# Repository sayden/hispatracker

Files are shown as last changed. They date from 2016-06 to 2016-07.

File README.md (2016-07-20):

# WIP hispatracker

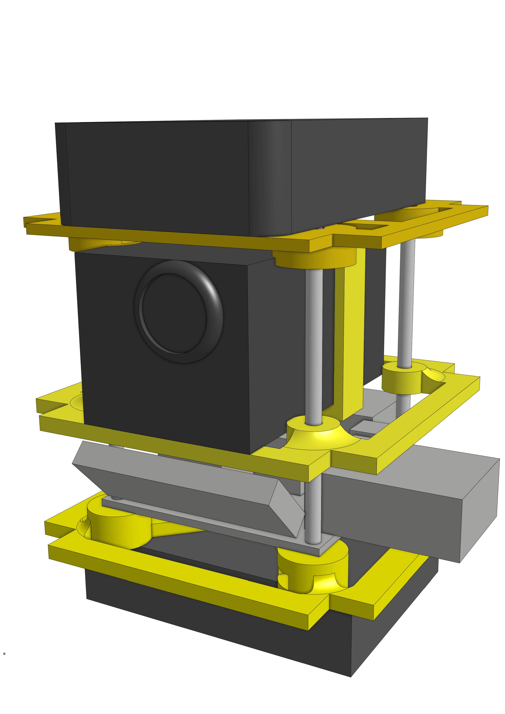
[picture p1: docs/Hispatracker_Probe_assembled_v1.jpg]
Hispatracker


An Arduino based project for High Altitude Ballooning. APRS tracker, 2xGPS, temperature and pressure. It still lacks SD logging and an external temperature sensor as the sketch was running out of memory. We are working in a improved version with the atmega1284p-pu to achieve this goals (and maybe some more).

## Sensors and libraries in use

### GPS and Altitude: Ublox Neo6M
We strongly recommend to use SlashDevin's [NeoGPS](https://github.com/SlashDevin/NeoGPS) library for its low memory footprint and awesome documentation. The alternative, TinyGPS is too heavy for most applications in a common Arduino (atmega328p-pu).

Our GPS is the Ublox Neo-6m with a performance of 50.000 meters (yes, 50 km) of altitude, 2.5 meters of accuracy and works at 3.3v

### BMP085 Temperature, altitude and pressure sensor

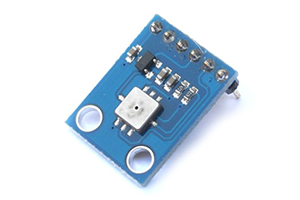
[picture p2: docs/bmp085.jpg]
BMP085


Good compromise between price and capabilities but with a altitude limit of 9000 meters over the sea (27000 feet). It works at 3.3v

### RF Transmission: Radiometrix HX1

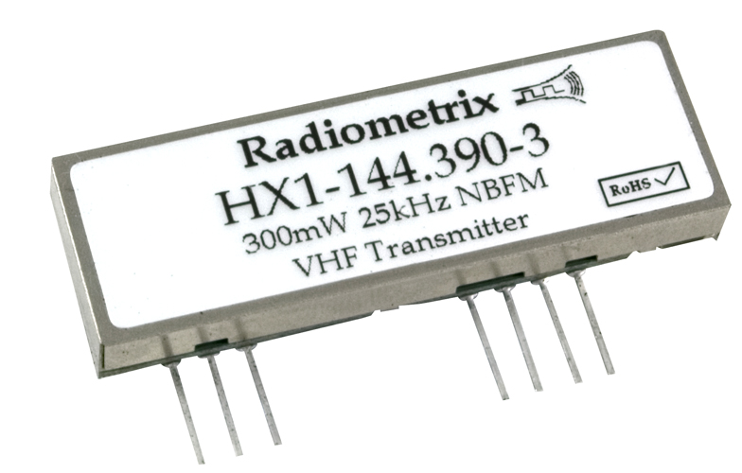
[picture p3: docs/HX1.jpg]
HX1


We think that maybe this was a mistake. It has a usable range over 10km and a consumption of 140mA. It has a transmit power of 300mW so you probably need HAM license to use it. Also it works at 5v, being the only module with this voltage needs, it has introduce a need of raising the VIN to, at least 6v so that we provide a regulated supply of 5v to the Radio and 3.3v to the rest of the module. Also it has force us to use a logic level converter to communicate to it. 

The good part is that it was the only able to transmit at 144.800 to use the APRS network. So we can use the network to track our payload with webs like [aprs.fi](http://aprs.fi).

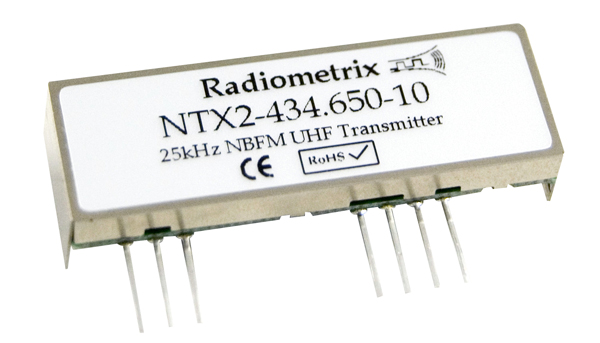
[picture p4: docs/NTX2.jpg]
NTX2


The alternative was to use the NTX2 transmitter. This transmitter is license free with a usable range of 500m (thats a 5% of the power of the HX1). It just transmits on 434.075MHz, 434.650MHz and 458.700MHz so it's not in the APRS network. It has a voltage regulator and you can feed it with 3.3 volts. We'll play with it in the future.

### Arduino Pro Mini 3.3v

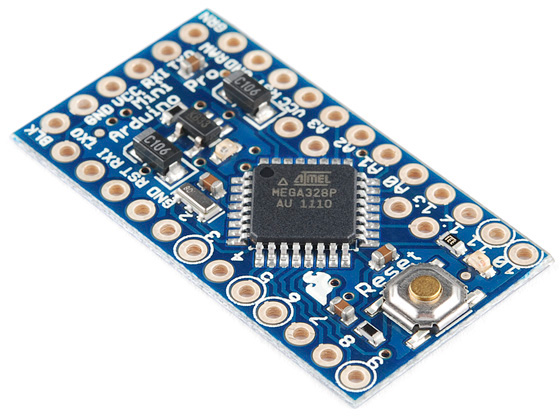
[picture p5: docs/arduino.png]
arduino


Finally, our brain is controlled by an Arduino Pro Mini running at 3.3v

### PCB
Our PCB has been specifically design to fit our needs. You'll find the files in the eagle folder. The PCB has been produce in Seeedstudio. It's 5x5 cm.

### Hardware

Check the [docs](docs) folder. We have used a Prusa i3 3D printer to build the frame of the probe. Basically supports for the batteries, camera, PCB and GPS tracker. STL's will be available in the hardware folder soon as well as in Thingiverse.

The supports are 7x7cm with holes to support the PCB of 5x5cm. In our first tests it reaches a height of 107mm.

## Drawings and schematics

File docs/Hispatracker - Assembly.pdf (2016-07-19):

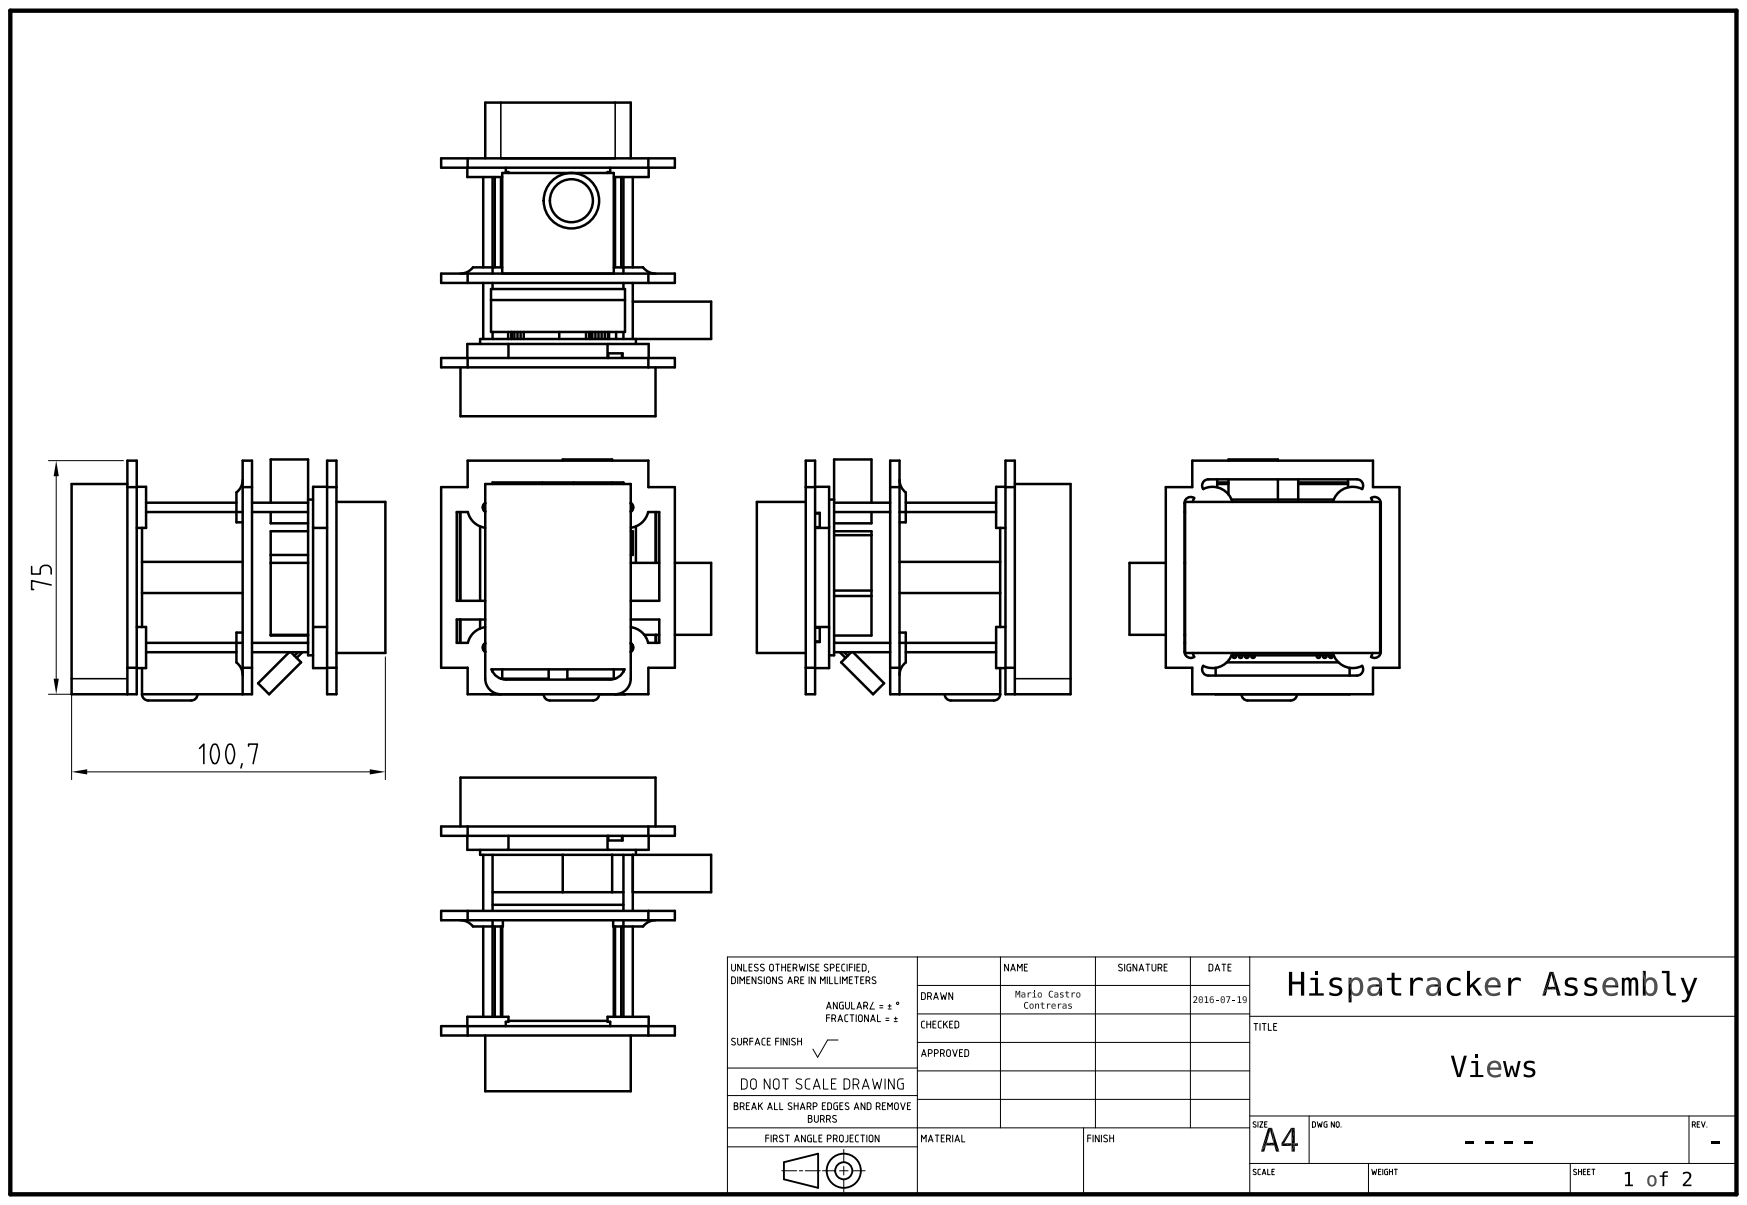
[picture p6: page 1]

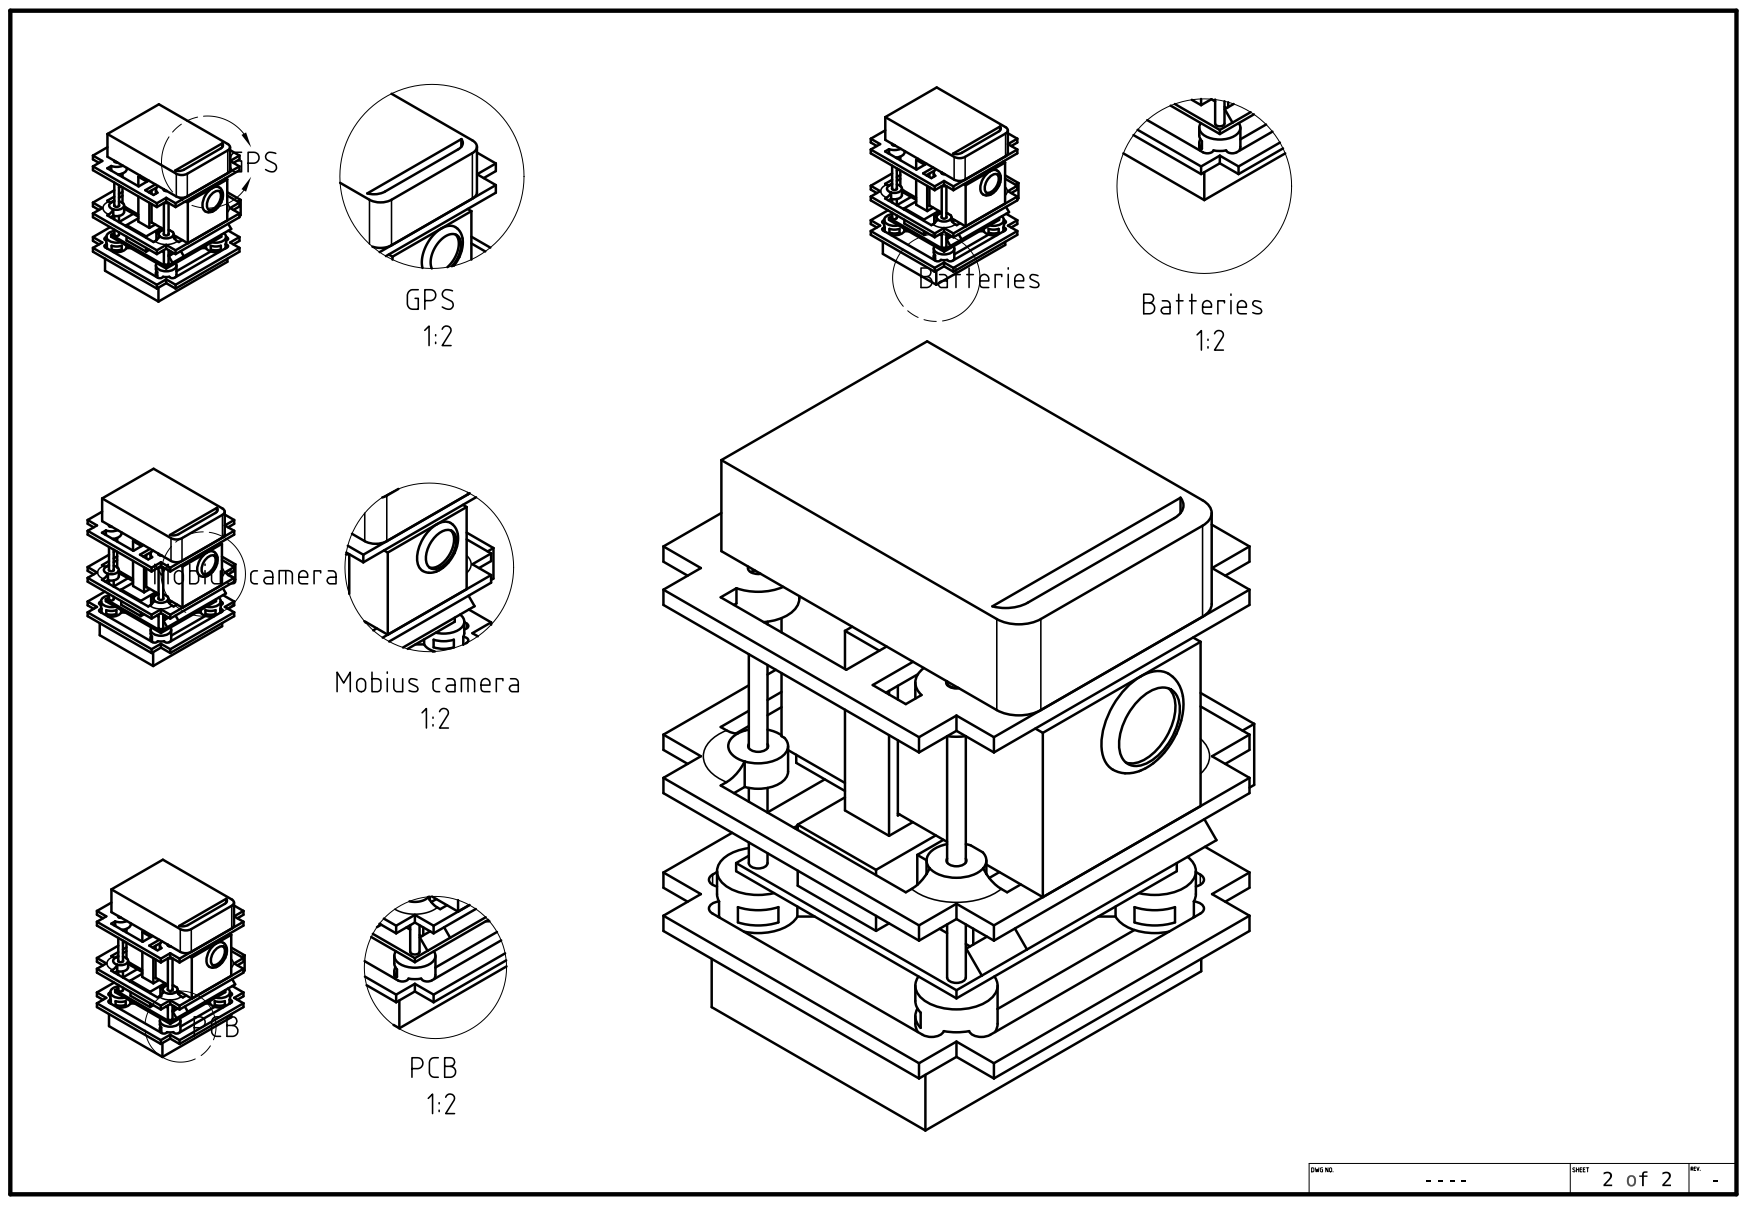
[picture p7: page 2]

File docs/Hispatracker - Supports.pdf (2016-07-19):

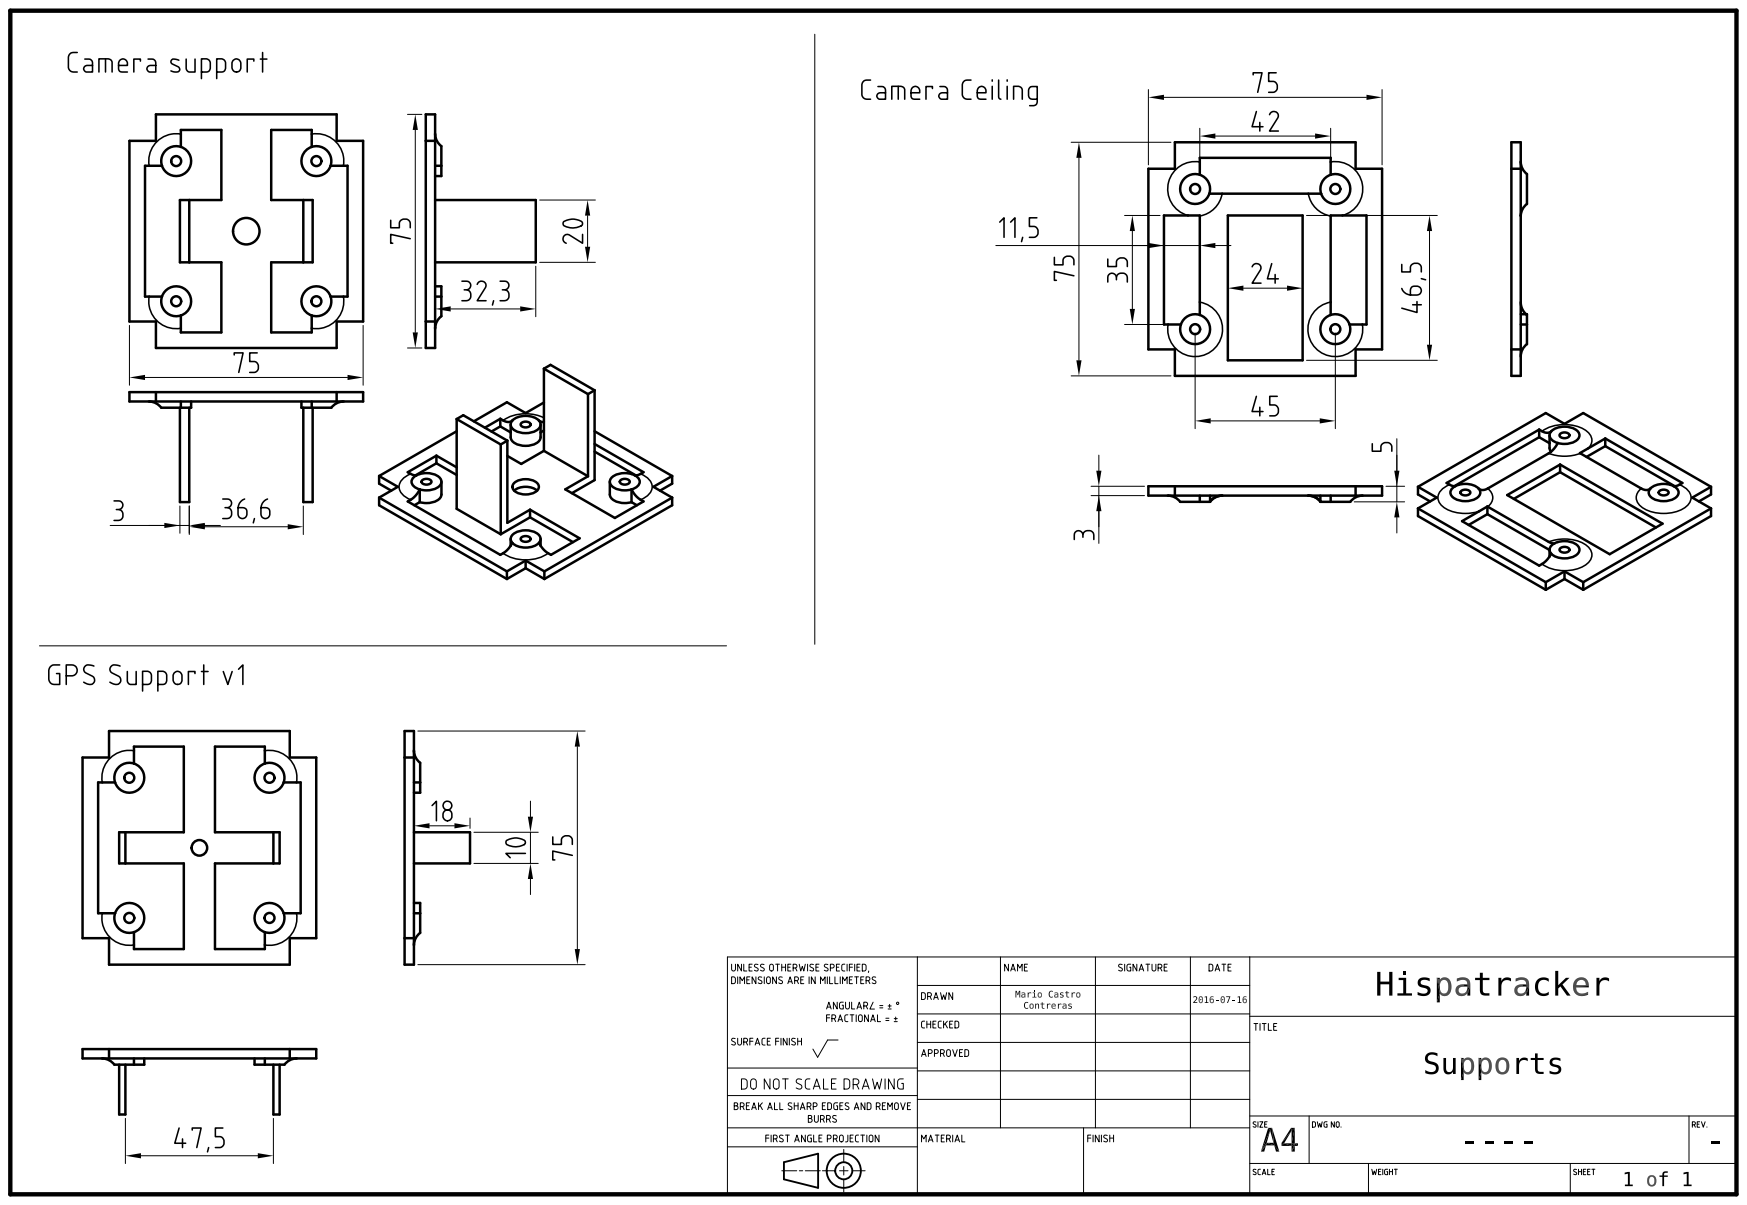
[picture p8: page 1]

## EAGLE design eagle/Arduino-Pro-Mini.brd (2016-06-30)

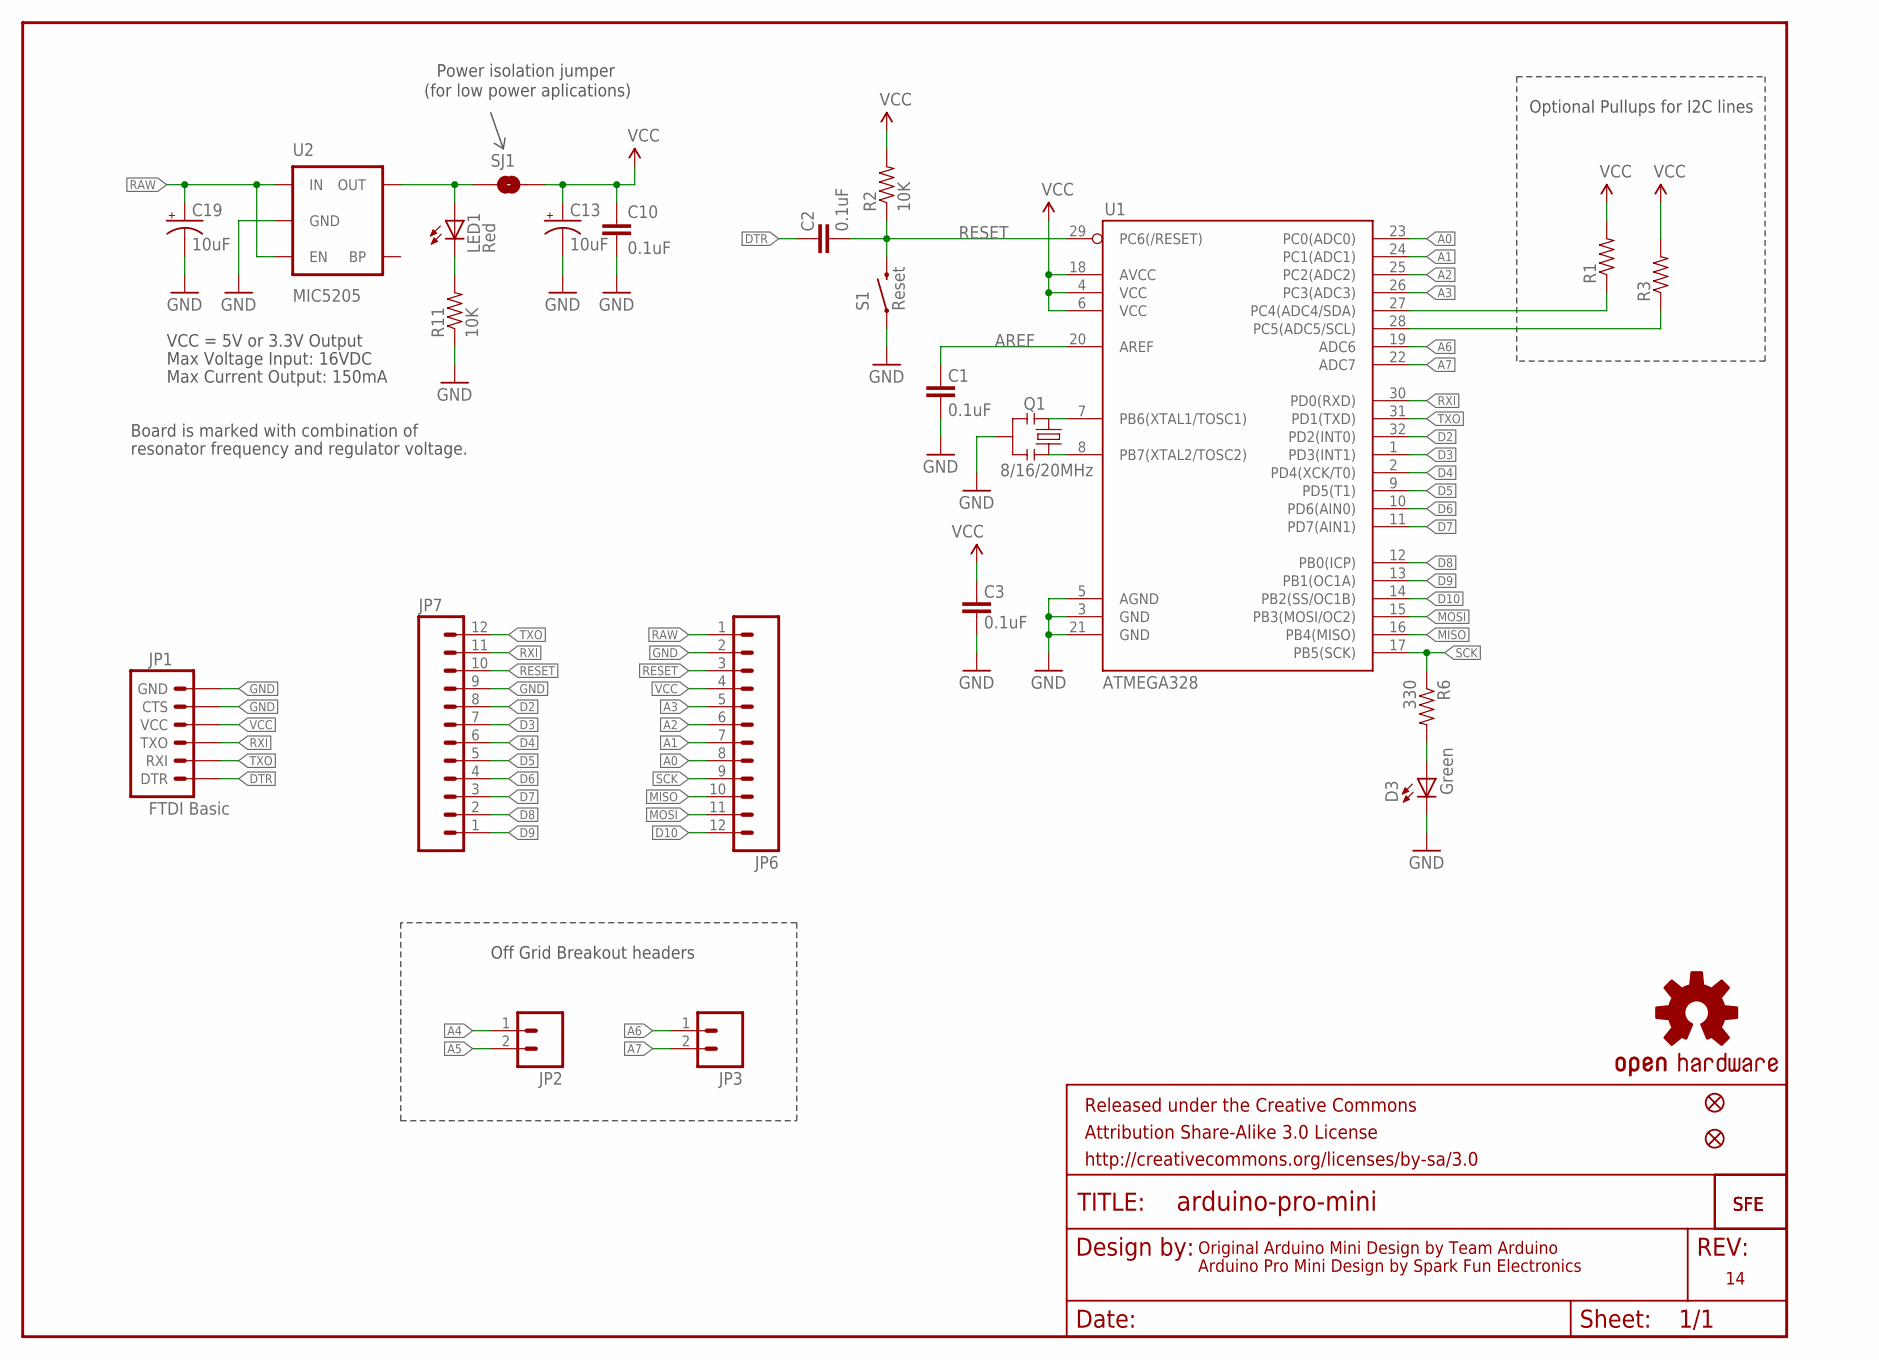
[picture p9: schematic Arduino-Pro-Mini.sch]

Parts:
C1, C2, C3, C10: 0.1uF; 0603-CAP
C13, C19: 10uF; EIA3216
D3: Green; 0603-LED-ALT1
FRAME1: FRAME-LETTER; CREATIVE_COMMONS
JP1: FTDI Basic; 1X06
JP2, JP3: M02PTH; 1X02
JP5, JP8: FIDUCIALUFIDUCIAL; MICRO-FIDUCIAL
JP6, JP7: M12PTH; 1X12
LED1: Red; 0603-LED-ALT1
Q1: 8/16/20MHz; RESONATOR-SMD-1:1
R1, R3: RESISTOR0603-RES; 0603-RES
R2, R11: 10K; 0603-RES
R6: 330; 0603-RES
S1: Reset; TACTILE-SWITCH-SMD-ALT01
SJ1: SOLDERJUMPERNC; SJ_2S
U1: ATMEGA328; TQFP32-08
U2: MIC5205; SOT23-5
U$1: LOGO-SFESK; SFE-LOGO-FLAME
U$3: OSHW-LOGOS; OSHW-LOGO-S
U$11: LOGO-SFENEW; SFE-NEW-WEBLOGO

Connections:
A0: JP6.8, U1.23 (PC0(ADC0))
A1: JP6.7, U1.24 (PC1(ADC1))
A2: JP6.6, U1.25 (PC2(ADC2))
A3: JP6.5, U1.26 (PC3(ADC3))
A4: JP2.1, R1.1, U1.27 (PC4(ADC4/SDA))
A5: JP2.2, R3.1, U1.28 (PC5(ADC5/SCL))
A6: JP3.1, U1.19 (ADC6)
A7: JP3.2, U1.22 (ADC7)
AREF: C1.2, U1.20 (AREF)
D2: JP7.8, U1.32 (PD2(INT0))
D3: JP7.7, U1.1 (PD3(INT1))
D4: JP7.6, U1.2 (PD4(XCK/T0))
D5: JP7.5, U1.9 (PD5(T1))
D6: JP7.4, U1.10 (PD6(AIN0))
D7: JP7.3, U1.11 (PD7(AIN1))
D8: JP7.2, U1.12 (PB0(ICP))
D9: JP7.1, U1.13 (PB1(OC1A))
D10: JP6.12, U1.14 (PB2(SS/OC1B))
DTR: C2.2, JP1.1 (DTR)
GND: C1.1, C3.1, C10.2, C13.C (-), C19.C (-), D3.C, JP1.5 (CTS), JP1.6 (GND), JP6.2, JP7.9, Q1.2, R11.1, S1.1, S1.2 (1), U1.3 (GND), U1.5 (AGND), U1.21 (GND), U2.2 (GND)
MISO: JP6.10, U1.16 (PB4(MISO))
MOSI: JP6.11, U1.15 (PB3(MOSI/OC2))
unnamed: Q1.3, U1.8 (PB7(XTAL2/TOSC2))
unnamed: Q1.1, U1.7 (PB6(XTAL1/TOSC1))
unnamed: LED1.A, SJ1.1, U2.5 (OUT)
unnamed: LED1.C, R11.2
unnamed: D3.A, R6.2
RAW: C19.A (+), JP6.1, U2.1 (IN), U2.3 (EN)
RESET: C2.1, JP6.3, JP7.10, R2.1, S1.3 (2), S1.4 (2), U1.29 (PC6(/RESET))
RXI: JP1.3 (TXO), JP7.11, U1.30 (PD0(RXD))
SCK: JP6.9, R6.1, U1.17 (PB5(SCK))
TXO: JP1.2 (RXI), JP7.12, U1.31 (PD1(TXD))
VCC: C3.2, C10.1, C13.A (+), JP1.4 (VCC), JP6.4, R1.2, R2.2, R3.2, SJ1.2, U1.4 (VCC), U1.6 (VCC), U1.18 (AVCC)

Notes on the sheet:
Original Arduino Mini Design by Team Arduino
Arduino Pro Mini Design by Spark Fun Electronics
Max Voltage Input: 16VDC
Max Current Output: 150mA
Board is marked with combination of
resonator frequency and regulator voltage.
VCC = 5V or 3.3V Output
Optional Pullups for I2C lines
Off Grid Breakout headers
Power isolation jumper
(for low power aplications)

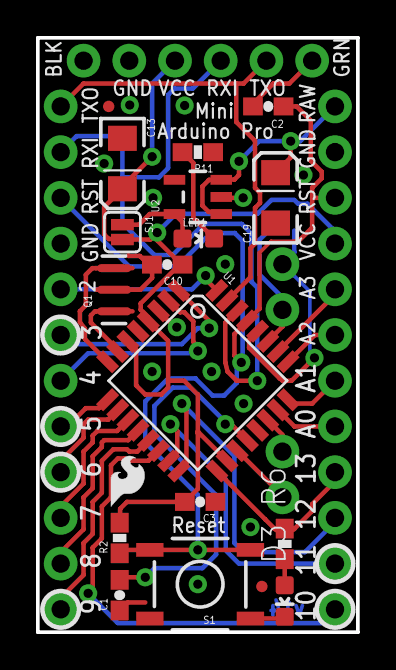
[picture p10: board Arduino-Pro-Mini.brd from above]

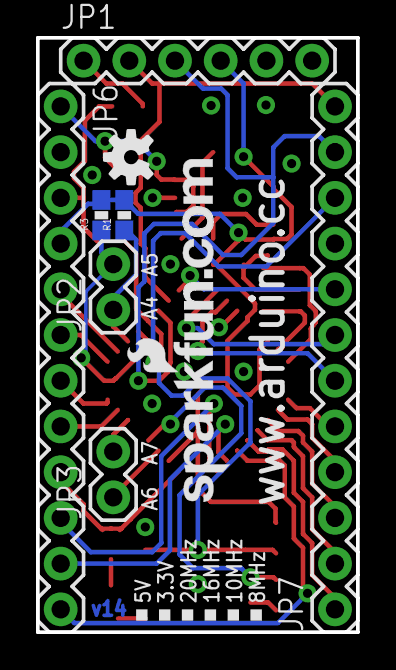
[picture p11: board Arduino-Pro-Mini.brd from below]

Board: 2 copper layers, 17.8 x 33.0 mm, 29 parts (9 on the bottom side), 33 nets.

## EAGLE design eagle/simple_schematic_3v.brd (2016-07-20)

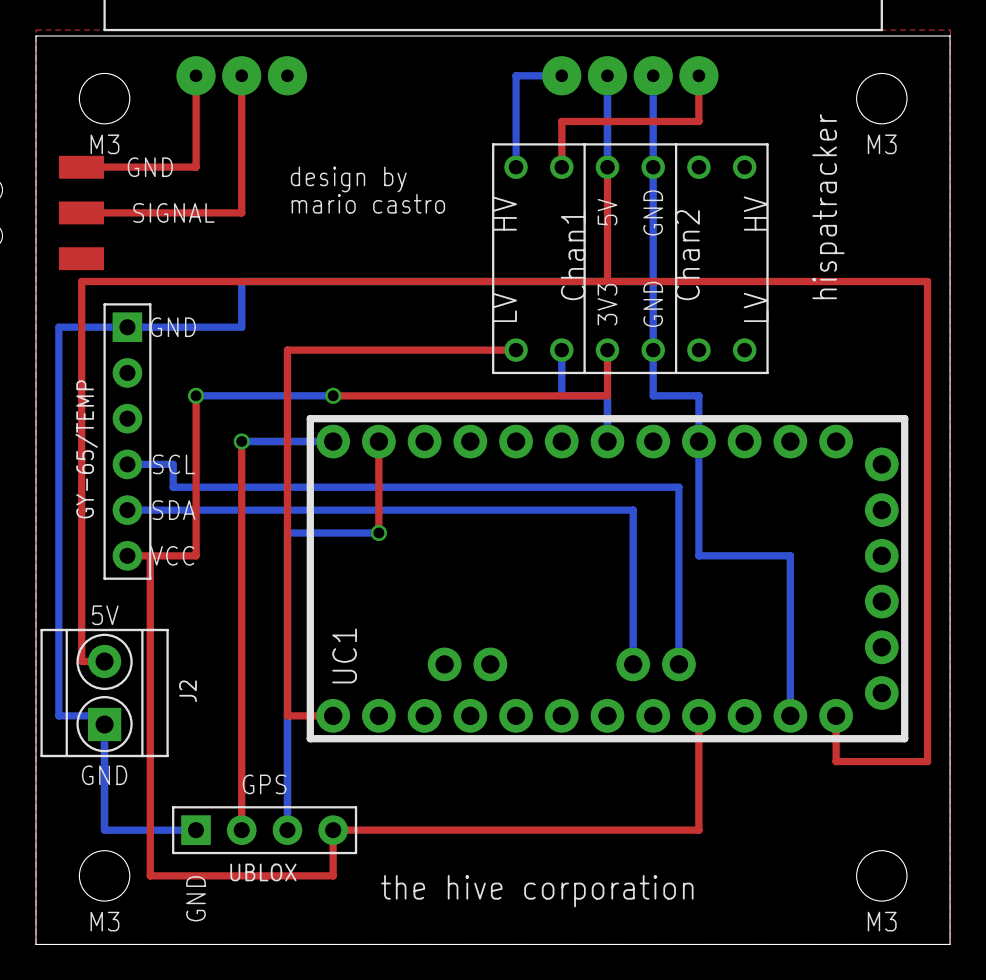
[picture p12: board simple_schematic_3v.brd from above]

Board: 2 copper layers, 50.8 x 50.5 mm, 7 parts (0 on the bottom side), 13 nets.

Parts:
GY-65/TEMP: 6p-2.54; H6-2.54
J1: 1X03_SMD_RA_MALE_POST_SMALLER
J2: GREEN-2P-3.5; H2-3.5-7.0X7.0MM
U$1: RADIOMETRIX-HX1
U$2: LOGIC_LEVEL_CONVERTER
UBLOX: 4p-2.54; H4-2.54
UC1: ARDUINO_PRO_MINI_3V3; ARDUINO_PRO_MINI

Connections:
3V3: GY-65/TEMP.6, U$2.P$3, UBLOX.4, UC1.21
5V: J2.2, U$1.VCC, U$2.P$10, UC1.24
GND: GY-65/TEMP.1, J2.1, U$1.0V, U$2.P$4, U$2.P$9, UBLOX.1, UC1.4, UC1.23
HX1_ENABLE: U$1.EN, U$2.P$12
HX1_EN_LOW: U$2.P$1, UC1.13
HX1_TXD: U$1.TXD, U$2.P$11
HX1_TXD_LOW: U$2.P$2, UC1.6
unnamed: J1.1, U$1.RFGND2
unnamed: J1.2, U$1.RFOUT
SCL: GY-65/TEMP.4, UC1.A5
SDA: GY-65/TEMP.5, UC1.A4
UBLOX_RX: UBLOX.2, UC1.12
UBLOX_TX: UBLOX.3, UC1.11

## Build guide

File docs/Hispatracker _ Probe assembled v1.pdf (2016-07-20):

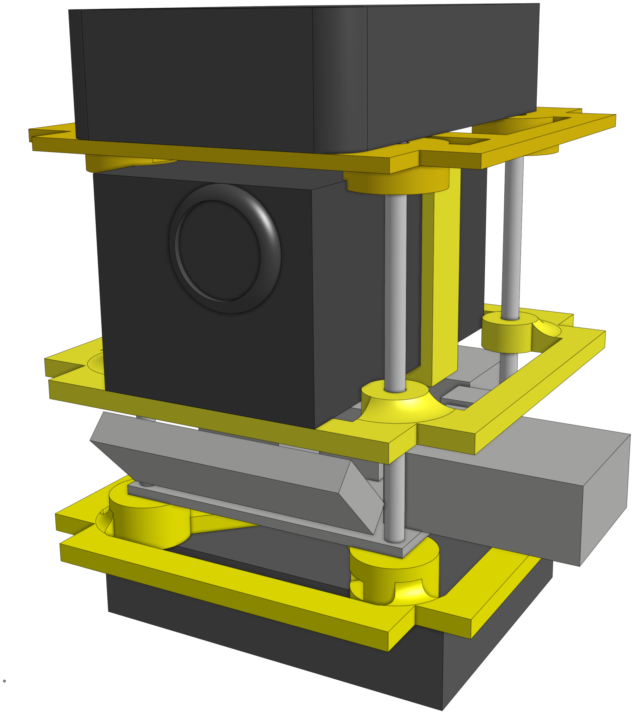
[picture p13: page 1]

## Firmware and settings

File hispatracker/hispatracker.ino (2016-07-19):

#include <Arduino.h>
#include "NMEAGPS.h"


#include "config.h"
#include "afsk_avr.h"
#include "aprs.h"
#include "pin.h"
#include "power.h"


#define LOAD_EEPROM

#include <AltSoftSerial.h>

#include "GPSport.h"
//------------------------------------------------------------
// This object parses received characters
//   into the gps.fix() data structure
static NMEAGPS  gps;

//------------------------------------------------------------
//  Define a set of GPS fix information.  It will
//  hold on to the various pieces as they are received from
//  an RMC sentence.  It can be used anywhere in your sketch.
static gps_fix  fix_data;

//This values counts when is moment to send a new message
static uint8_t next_aprs = 0;

//Sends an APRS packet every...
#define SEND_TIME_SPACING 10
static APRSPacket packet;


//Internal Temp sensor
#include <Wire.h>
#include <Adafruit_BMP085.h>  // Adafruit BMP085 library

Adafruit_BMP085 bmp;


//--------------------------
// APRS Compression table is stored in the EEPROM to save some space
#ifdef LOAD_EEPROM
    #include "eeprom_loader.cpp"
#endif

void setup()
{  
  #ifdef LOAD_EEPROM
      loadEEPROM();
  #endif


  pinMode(LED_PIN, OUTPUT);
  pin_write(LED_PIN, LOW);

  bmp.begin();

  afsk_setup();

  // Start the UART for the GPS device
  gps_port.begin( 9600 );
}


static void doSomeWork() {
  packet.aprs_send();

  while (afsk_flush()) {
    power_save();
  }
  
} // doSomeWork

void getDatetimeReading(){
  char datetime[7];
  snprintf(datetime, 7, "%02d%02d%02d", fix_data.dateTime.hours, fix_data.dateTime.minutes, fix_data.dateTime.seconds);
  packet.setDatetime(datetime);
}

void getBMPReadings(){
  packet.setAltitude(bmp.readAltitude(101900));
  packet.setTemperature(bmp.readTemperature());
  packet.setPressure(bmp.readPressure());
}

void getSpeed(){
  int speed = pow(1.08,fix_data.speed()) - 1;
  packet.setSpeed(EEPROM.read(speed+33));
}

void getHeading(){
  int course = fix_data.heading() / 4.0;
  char c = EEPROM.read(course+33);
  packet.setHeading(c);
}


//Takes a floating point value of longitude and returns its corresponding 4 char value
//in APRS compressed format
void getLongitude(float l, char temp[5]){
    unsigned long res = 190463 * (180.0 + l);

    uint32_t res1 = res/753571;
    uint32_t rem1 = res%753571;
    uint32_t res2 = rem1/8281;
    uint32_t rem2 = rem1%8281;
    uint16_t res3 = rem2/91;
    uint16_t rem3 = rem2%91;

    sprintf(temp, "%c%c%c%c\0", EEPROM.read(res1+33), EEPROM.read(res2+33), EEPROM.read(res3+33), EEPROM.read(rem3+33));
}

//Takes a floating point value of latitude and returns its corresponding 4 char value
//in APRS compressed format
void getLatitude(float l, char temp[5]){
    unsigned long res = 380926 * (90 - l);

    uint32_t res1 = res/753571;
    uint32_t rem1 = res%753571;
    uint32_t res2 = rem1/8281;
    uint32_t rem2 = rem1%8281;
    uint16_t res3 = rem2/91;
    uint16_t rem3 = rem2%91;

    sprintf(temp, "%c%c%c%c\0", EEPROM.read(res1+33), EEPROM.read(res2+33), EEPROM.read(res3+33), EEPROM.read(rem3+33));
}

static char latitude[5];
static char longitude[5];

void getLatitude(){
  getLatitude(fix_data.latitude(), latitude);
  packet.setLatitude(latitude);
}

void getLongitude(){
  getLongitude(fix_data.longitude(), longitude);
  packet.setLongitude(longitude);
}

//--------------------------

void loop()
{
  while (gps.available( gps_port )) {
    fix_data = gps.read();
    switch(next_aprs){
      case SEND_TIME_SPACING-5:
        getBMPReadings();
        break;
      case SEND_TIME_SPACING-4:
        if(fix_data.valid.speed) getSpeed();
        break;
      case SEND_TIME_SPACING-3:
        if(fix_data.valid.heading) getHeading();
        break;
      case SEND_TIME_SPACING-2:
        getDatetimeReading();
        break;
      case SEND_TIME_SPACING-1:
        if(fix_data.valid.location) {
          getLatitude();
          getLongitude();
        }
        break;
      case SEND_TIME_SPACING:
        doSomeWork();
        next_aprs=-1;
        break;
      default:
        break;
    }
    next_aprs++;
  }
}

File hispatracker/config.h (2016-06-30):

#ifndef __CONFIG_H__
#define __CONFIG_H__

// --------------------------------------------------------------------------
// APRS config (aprs.c)
// --------------------------------------------------------------------------

// Set your callsign and SSID here. Common values for the SSID are
// (from http://zlhams.wikidot.com/aprs-ssidguide):
//
// - Balloons:  11
// - Cars:       9
// - Home:       0
// - IGate:      5
 #define S_CALLSIGN      "HIPH"
 #define S_CALLSIGN_ID   11

// Destination callsign: APRS (with SSID=0) is usually okay.
 #define D_CALLSIGN      "APRS"
 #define D_CALLSIGN_ID   0

// Digipeating paths:
// (read more about digipeating paths here: http://wa8lmf.net/DigiPaths/ )
// The recommended digi path for a balloon is WIDE2-1 or pathless. The default
// is pathless. Uncomment the following two lines for WIDE2-1 path:
 #define DIGI_PATH1      "WIDE2"
 #define DIGI_PATH1_TTL  1

// --------------------------------------------------------------------------
// AX.25 config (ax25.cpp)
// --------------------------------------------------------------------------

// TX delay in milliseconds
#define TX_DELAY      300

// --------------------------------------------------------------------------
// Tracker config (trackuino.pde)
// --------------------------------------------------------------------------

// APRS packets are slotted so that multiple trackers can be used without
// them stepping on one another. The transmission times are governed by
// the formula:
//
//         APRS_SLOT (seconds) + n * APRS_PERIOD (seconds)
//
// When launching multiple balloons, use the same APRS_PERIOD in all balloons
// and set APRS_SLOT so that the packets are spaced equally in time.
// Eg. for two balloons and APRS_PERIOD = 60, set APRS_SLOT to 0 and 30, 
// respectively. The first balloon will transmit at 00:00:00, 00:01:00, 
// 00:02:00, etc. and the second balloon will transmit at 00:00:30, 00:01:30,
// 00:02:30, etc.
#define APRS_SLOT     -1     // seconds. -1 disables slotted transmissions
#define APRS_PERIOD   30    // seconds

// GPS baud rate (in bits per second). This is also the baud rate at which
// debug data will be printed out the serial port.
#define GPS_BAUDRATE  9600


// --------------------------------------------------------------------------
// Modem config (afsk.cpp)
// --------------------------------------------------------------------------

// AUDIO_PIN is the audio-out pin. The audio is generated by timer 2 using
// PWM, so the only two options are pins 3 and 11.
// Pin 11 doubles as MOSI, so I suggest using pin 3 for PWM and leave 11 free
// in case you ever want to interface with an SPI device.
#define AUDIO_PIN       3

// Pre-emphasize the 2200 tone by 6 dB. This is actually done by 
// de-emphasizing the 1200 tone by 6 dB and it might greatly improve
// reception at the expense of poorer FM deviation, which translates
// into an overall lower amplitude of the received signal. 1 = yes, 0 = no.
#define PRE_EMPHASIS    0

// --------------------------------------------------------------------------
// Serial config
// --------------------------------------------------------------------------
#define RXPIN 8
#define TXPIN 9

// --------------------------------------------------------------------------
// Radio config (radio_hx1.cpp)
// --------------------------------------------------------------------------

// This is the PTT pin
#define PTT_PIN           10

// --------------------------------------------------------------------------
// Sensors config (sensors.cpp)
// --------------------------------------------------------------------------

// Most of the sensors.cpp functions use internal reference voltages (either
// AVCC or 1.1V). If you want to use an external reference, you should
// uncomment the following line:
//
// #define USE_AREF
//
// BEWARE! If you hook up an external voltage to the AREF pin and 
// accidentally set the ADC to any of the internal references, YOU WILL
// FRY YOUR AVR.
//
// It is always advised to connect the AREF pin through a pull-up resistor,
// whose value is defined here in ohms (set to 0 if no pull-up):
//
#define AREF_PULLUP           4700
//
// Since there is already a 32K resistor at the ADC pin, the actual
// voltage read will be VREF * 32 / (32 + AREF_PULLUP)
//
// Read more in the Arduino reference docs:
// http://arduino.cc/en/Reference/AnalogReference?from=Reference.AREF

// Pin mappings for the internal / external temperature sensors. VS refers
// to (arduino) digital pins, whereas VOUT refers to (arduino) analog pins.
#define INTERNAL_LM60_VS_PIN     8
#define INTERNAL_LM60_VOUT_PIN   0
#define EXTERNAL_LM60_VS_PIN     7
#define EXTERNAL_LM60_VOUT_PIN   1

// Units for temperature sensors (Added by: Kyle Crockett)
// 1 = Celsius, 2 = Kelvin, 3 = Fahrenheit
#define TEMP_UNIT 1

// Calibration value in the units selected. Use integer only.
#define CALIBRATION_VAL 0
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

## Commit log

2016-06-25 Added internal and external temperature sensor
2016-06-26 APRS message sending working version with SD implementation that doesn't work yet.
    [afsk_avr.cpp, config.h]
2016-06-28 Still doesn't work. I think it's a memory issue
    [config.h, hispatracker.ino]
2016-06-30 SD Card and external temperature removed. Eagle files added
    [Arduino-Pro-Mini.brd, Arduino-Pro-Mini.sch, schematic.sch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]
2016-06-30 Almost working version with APRS message format fixed and more accuracy on extra.
    [hispatracker.ino]
2016-07-02 Seems it's working finally.... but consuming a lot of current
2016-07-20 README and Eagle files updated. Images uploaded
    [simple_schematic_3v.brd]

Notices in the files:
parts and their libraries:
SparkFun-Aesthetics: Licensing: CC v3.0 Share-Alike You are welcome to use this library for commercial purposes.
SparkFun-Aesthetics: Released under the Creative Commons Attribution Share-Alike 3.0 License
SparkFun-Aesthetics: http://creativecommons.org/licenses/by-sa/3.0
